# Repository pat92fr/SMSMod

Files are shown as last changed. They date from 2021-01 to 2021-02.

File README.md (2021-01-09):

https://hackaday.io/project/176678-smarter-micro-servo-sms-mod

# SMSMod
 Smarter Micro Servo (SMS) MOD

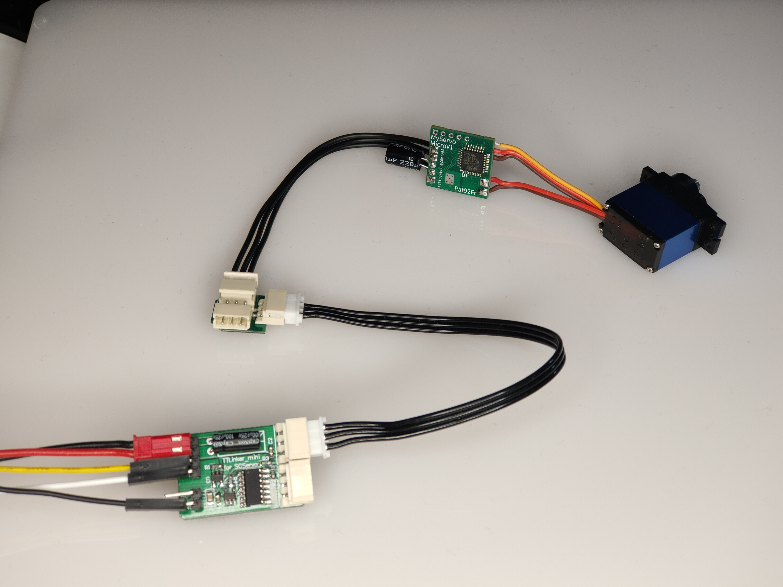
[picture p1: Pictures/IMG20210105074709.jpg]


This projet is a tiny control board for micro servo. It replaces the original servo control board and provides a smart bus interface (TTL level, Up to 1Mbps) and configurable close-loop regulation for robotic applications. Any micro and mini servo may be hacked and driven by this board (5-pin interface : 2 for DC motor, 3 for potentiometer). The control board may be directly powered by a LIPo 2S battery (min 6.5V, max 10V). 

Commercial off-the-shelf smart 3-pin cables, hubs, accessories and physical interface adapter boards (e.g. TTLinker) may be used to connect the hacked servo to the host controller (Arduino board, Arm-based board, RPi, and Jetson). User can drive up to 254 servo, with the same bus.

Position, velocity, and torque of each servo are controlable. Present position, velocity, and torque feedback are avaible. Communication protocol is developed in Python and C/C++ (Arduino). Ping, read, write, sync write, reboot, factory reset commands are supported. One command takes about 1ms to be processed with a return status.

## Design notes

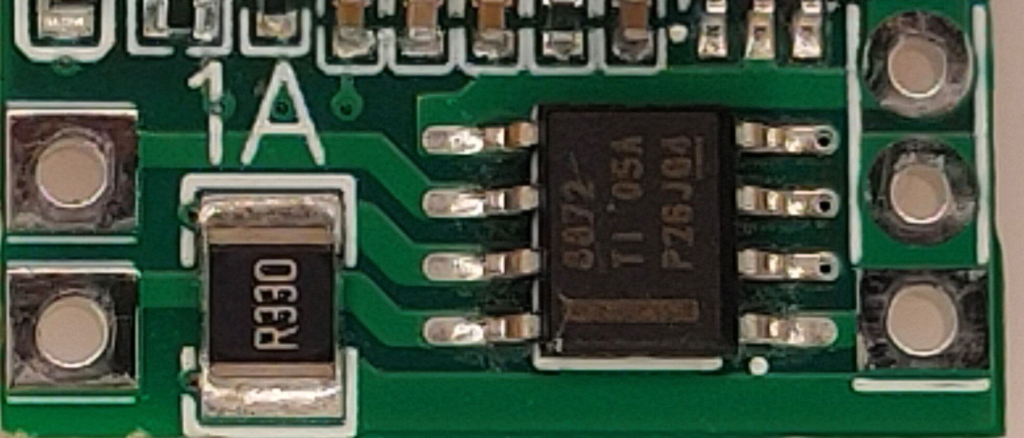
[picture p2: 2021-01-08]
Pictures/IMG20210104151520drv.jpg

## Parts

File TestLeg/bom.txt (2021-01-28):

2x MG92b/MG90s + accessories (screws, arms)
4x printed parts (femur and tibia, supportHipLegx2 one normal, one mirror)
3x screw+bolt M3 x 36mm (for support)
2x rod end bearing M3 x M3 (for linkage knee)
1x rod M3 x 36mm (for linkage knee)
2x 3-part thrust bearing 4x9x4mm (for knee)
1x screw+bolt M3 x 25mm (for knee)
1x M2 x 8 scree (fixing hip servo arm to femur)

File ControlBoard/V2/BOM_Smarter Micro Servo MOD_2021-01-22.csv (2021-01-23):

ID | Name | Designator | Footprint | Quantity | Manufacturer Part | Manufacturer | Supplier | Supplier Part | LCSC Assembly | JLCPCB SMD
1 | 22k | R7,R10 | R0402 | 2 | 0402WGF2202TCE | UniOhm | LCSC | C25768
2 | 2.2k | R3,R11 | R0402 | 2 | 0402WGF2201TCE | UniOhm | LCSC | C25879
3 | 1.5k | R2 | R0402 | 1 | 0402WGF1501TCE | UniOhm | LCSC | C25867
4 | 100k | R6 | R0402 | 1 | 0402WGF1003TCE | UniOhm | LCSC | C25741
5 | 47R | R5 | R0402 | 1 | 0402WGF470JTCE | UniOhm | LCSC | C25118
6 | 200 | R4 | R0402 | 1 | 0402WGF2000TCE | UniOhm | LCSC | C25087
7 | DRV8872DDAR | U3 | HSOP-8_L5.0-W4.0-P1.27-LS6.2-BL-EP | 1 | DRV8872DDAR | TI | LCSC | C114179 | Yes
8 | LED-0603_R | LED2 | LED0603_RED | 1 | 19-213/Y2C-CQ2R2L/3T(CY) | EVERLIGHT | LCSC | C72038
9 | STM32G431K8T6 | U1 | LQFP-32_L7.0-W7.0-P0.80-LS9.0-BL | 1 | STM32G431KBT6 | STMicroelectronics | LCSC | C529357
10 | HDR-M-2.54_1x1 | J4,J3 | HDR-M-2.54_1X1 | 2 |  |  | LCSC | C81276
11 | 0.33R | R1 | R1210 | 1 | 1210W2F330LT5E | Uniroyal Elec | LCSC | C95211 | Yes
12 | TLV70433DBVT | U2 | TSOT-23-5_L2.9-W1.6-P0.95-LS2.8-BR | 1 | TLV70433DBVT | Texas Instruments | LCSC | C94776 |  | Yes
13 | 10uH | L1 | L0603 | 1 | LBMF1608T100K | TAIYO YUDEN | LCSC | C87216
14 | HDR-F-2.54_1x3 | H3 | HDR-F-2.54_1X3 | 1 |  |  | LCSC | C146690
15 | HDR-M-2.54_1x5 | J2,J1 | HDR-M-2.54_1X5 | 2 |  |  | LCSC | C358687
16 | NC7SP125P5X | U6,U5 | SC-70-5_L2.1-W1.3-P0.65-LS2.1-BR | 2 | NC7SP125P5X | ON Semicon | LCSC | C184652 | Yes
17 | 100nF | C5,C4,C10,C9,C7,C3 | C0402 | 6 | CL05B104KO5NNNC | SAMSUNG | LCSC | C1525
18 | 1nF | C13 | C0402 | 1 | 0402B102K500NT | FH | LCSC | C1523
19 | 1uF | C12,C1 | C0402 | 2 | CL05A105KA5NQNC | SAMSUNG | LCSC | C52923
20 | 10nF | C11 | C0402 | 1 | CL05B103KB5NNNC | SAMSUNG | LCSC | C15195
21 | 4.7uF | C8,C2 | C0402 | 2 | CL05A475MP5NRNC | SAMSUNG | LCSC | C23733

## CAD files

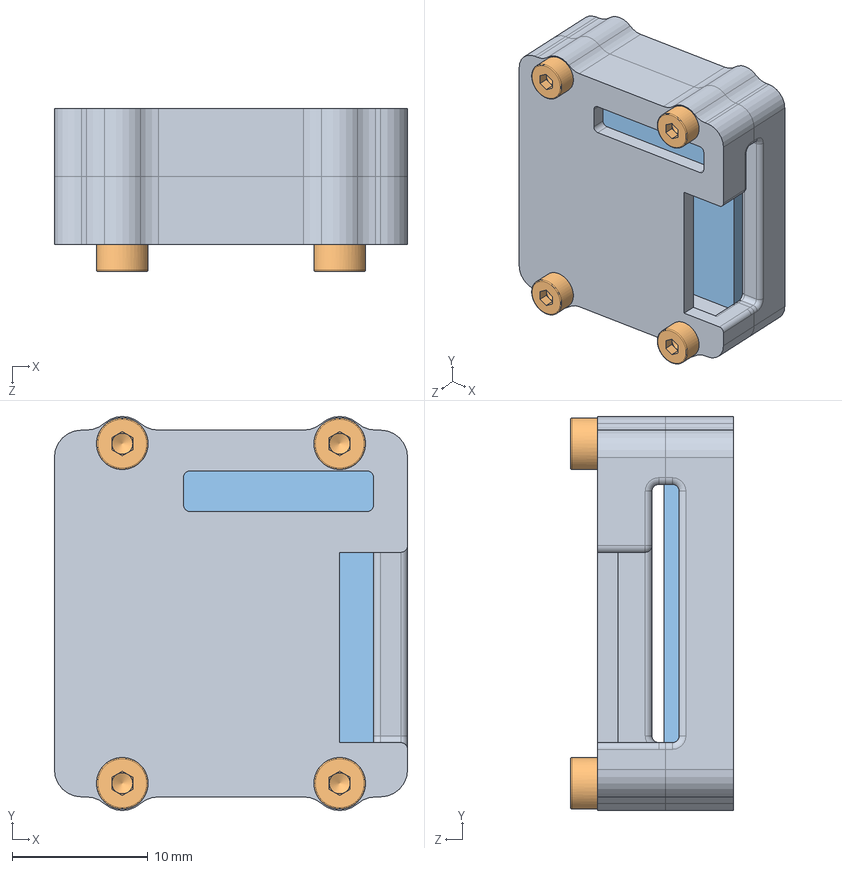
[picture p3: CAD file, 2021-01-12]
ControlBoard/CASE/Assemblage.SLDASM
26.0 x 29.0 x 12.0 mm
case x 2
socket head cap screw_iso x 4
PCB

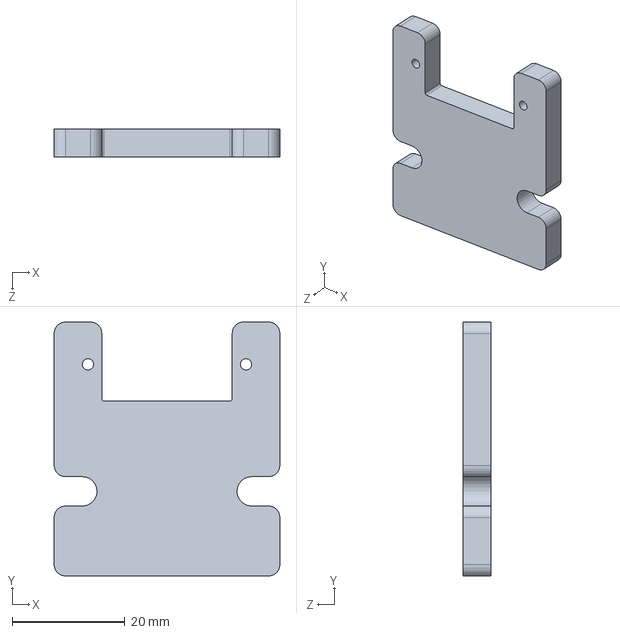
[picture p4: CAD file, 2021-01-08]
ControlBoard/MECA/supportMicro.SLDPRT
40.0 x 45.0 x 5.00 mm

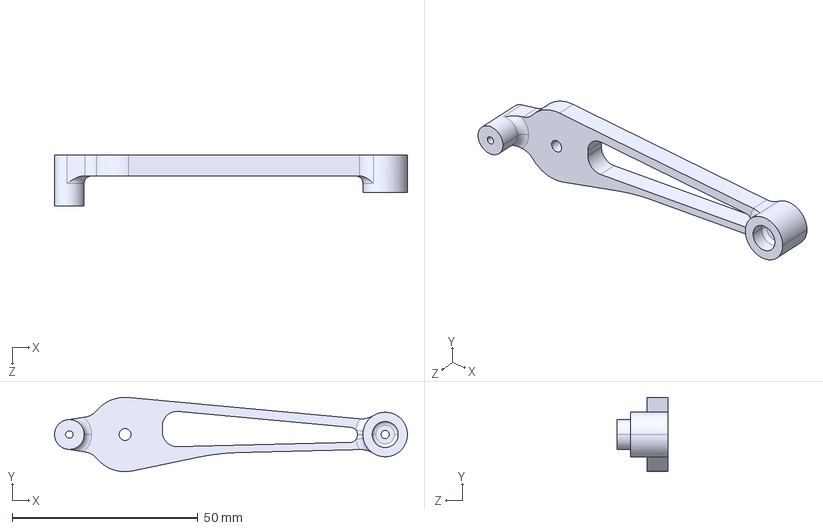
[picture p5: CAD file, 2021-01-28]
TestLeg/Tibia3.STEP
95.0 x 20.0 x 13.6 mm

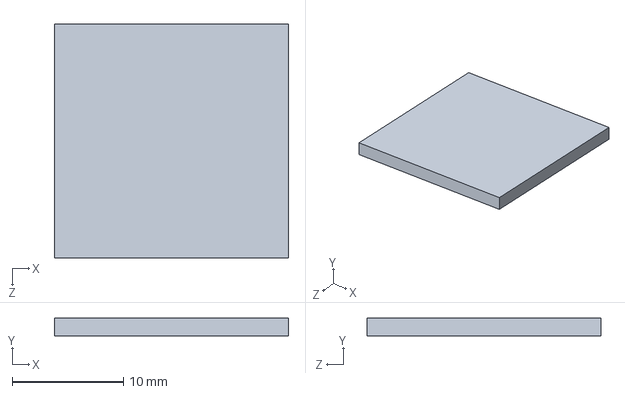
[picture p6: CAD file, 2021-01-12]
ControlBoard/CASE/PCB.SLDPRT
21.0 x 1.60 x 21.0 mm

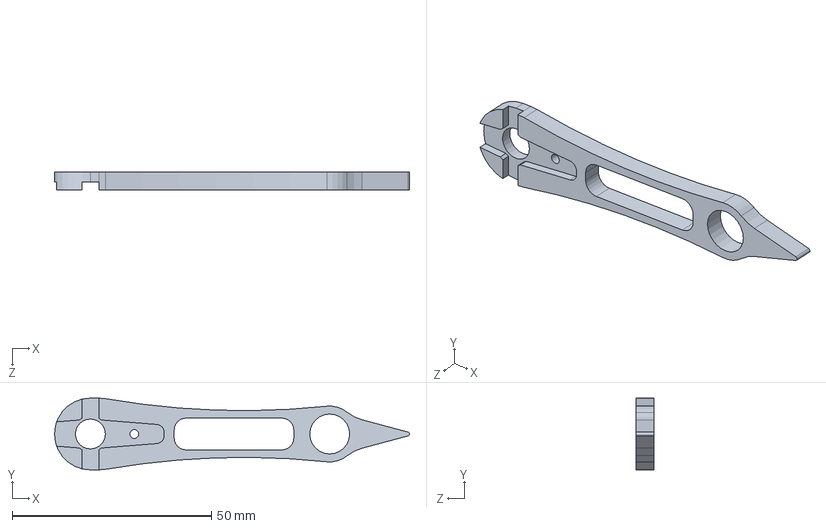
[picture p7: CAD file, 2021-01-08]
ControlBoard/MECA/Arm.SLDPRT
89.0 x 18.0 x 4.60 mm

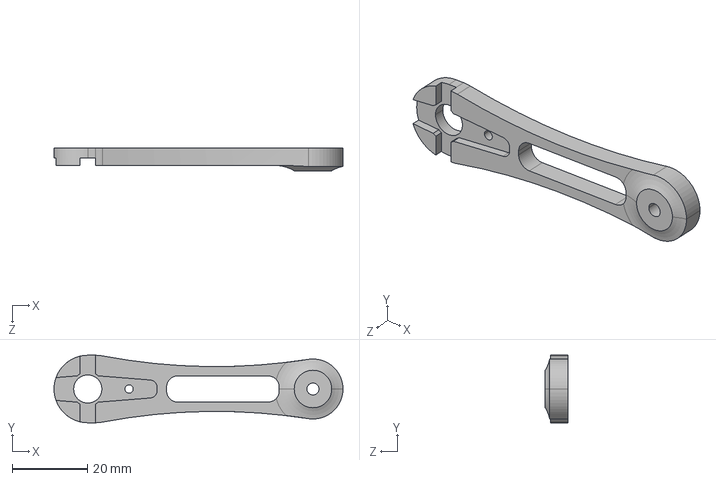
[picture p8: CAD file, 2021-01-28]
TestLeg/Femur4.STEP
77.0 x 18.0 x 6.00 mm

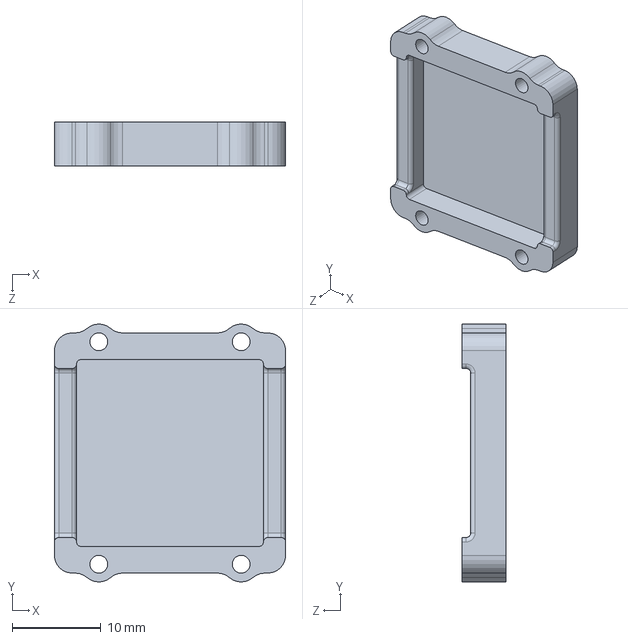
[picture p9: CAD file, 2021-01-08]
ControlBoard/CASE/case.SLDPRT
26.0 x 29.0 x 5.00 mm

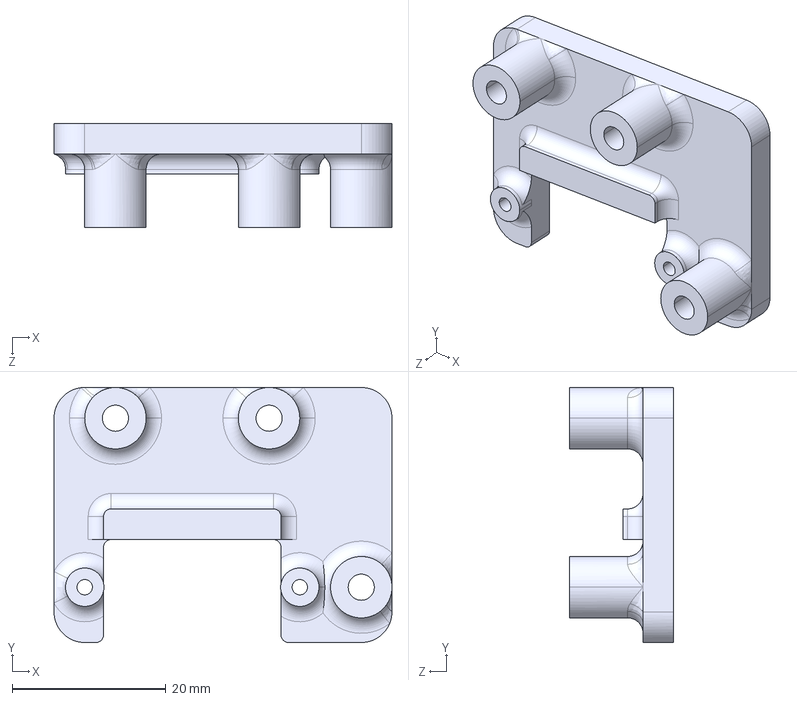
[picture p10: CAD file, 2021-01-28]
TestLeg/supportHipLeg.STEP
44.0 x 33.2 x 13.6 mm

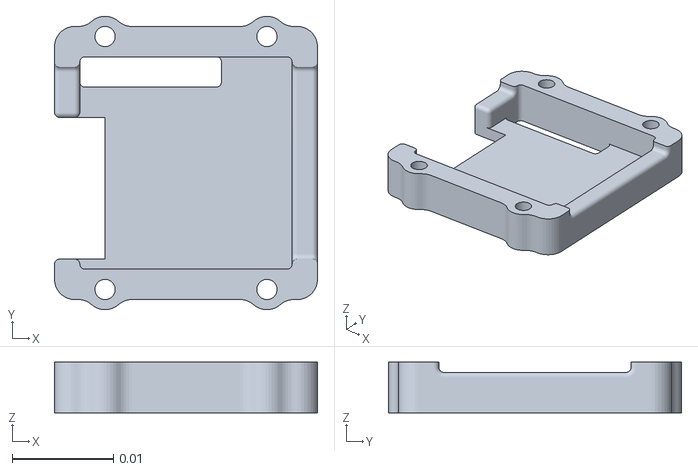
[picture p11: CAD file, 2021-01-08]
ControlBoard/CASE/caseTOP.STL
0.026 x 0.029 x 0.005

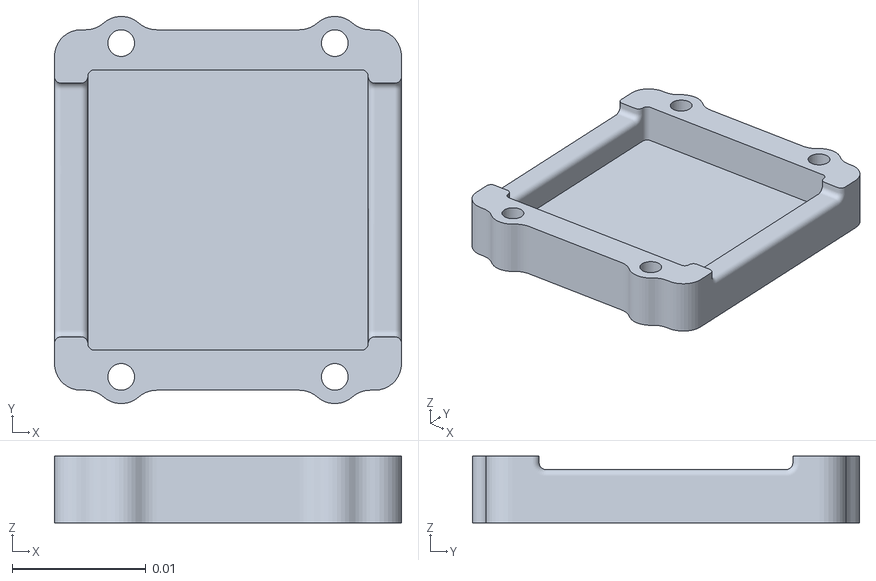
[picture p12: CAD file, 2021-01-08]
ControlBoard/CASE/caseBOTTOM.STL
0.026 x 0.029 x 0.005

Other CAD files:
ControlBoard/MECA/Arm.STL
TestLeg/Femur4.STL
TestLeg/Tibia3.STL
TestLeg/supportHipLeg.STL

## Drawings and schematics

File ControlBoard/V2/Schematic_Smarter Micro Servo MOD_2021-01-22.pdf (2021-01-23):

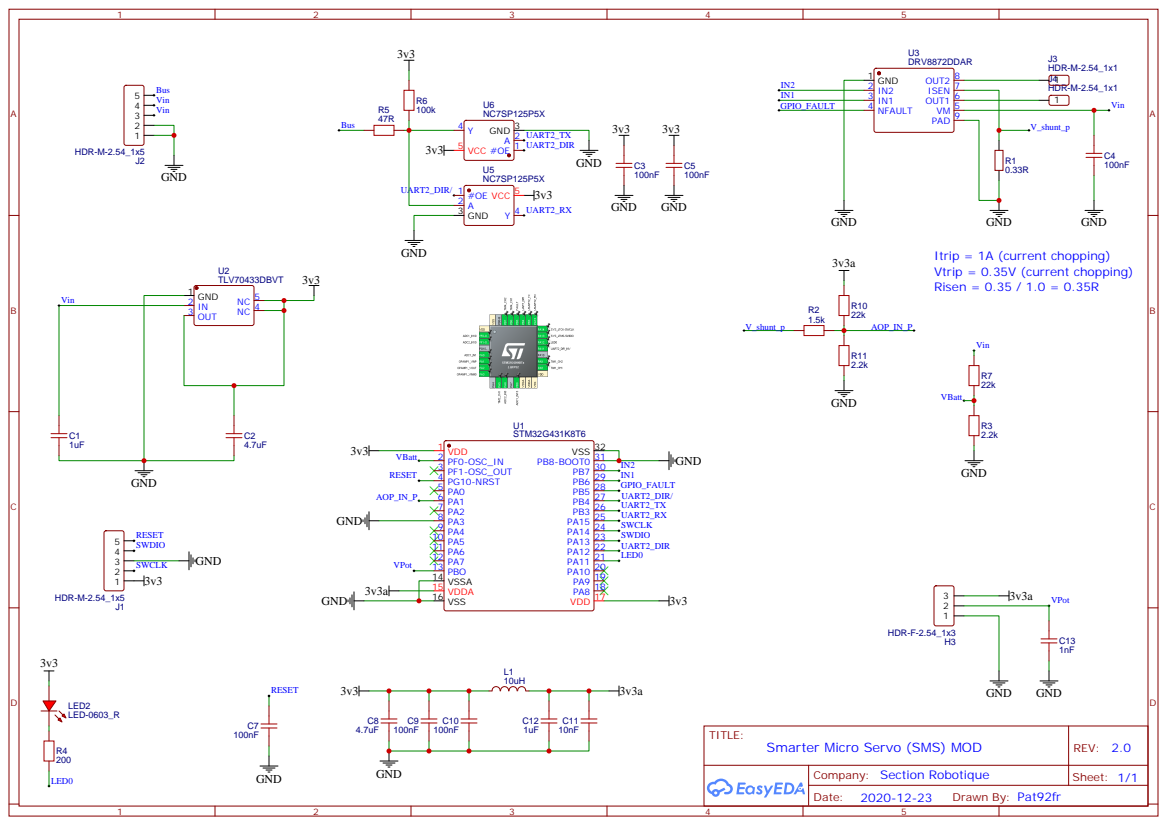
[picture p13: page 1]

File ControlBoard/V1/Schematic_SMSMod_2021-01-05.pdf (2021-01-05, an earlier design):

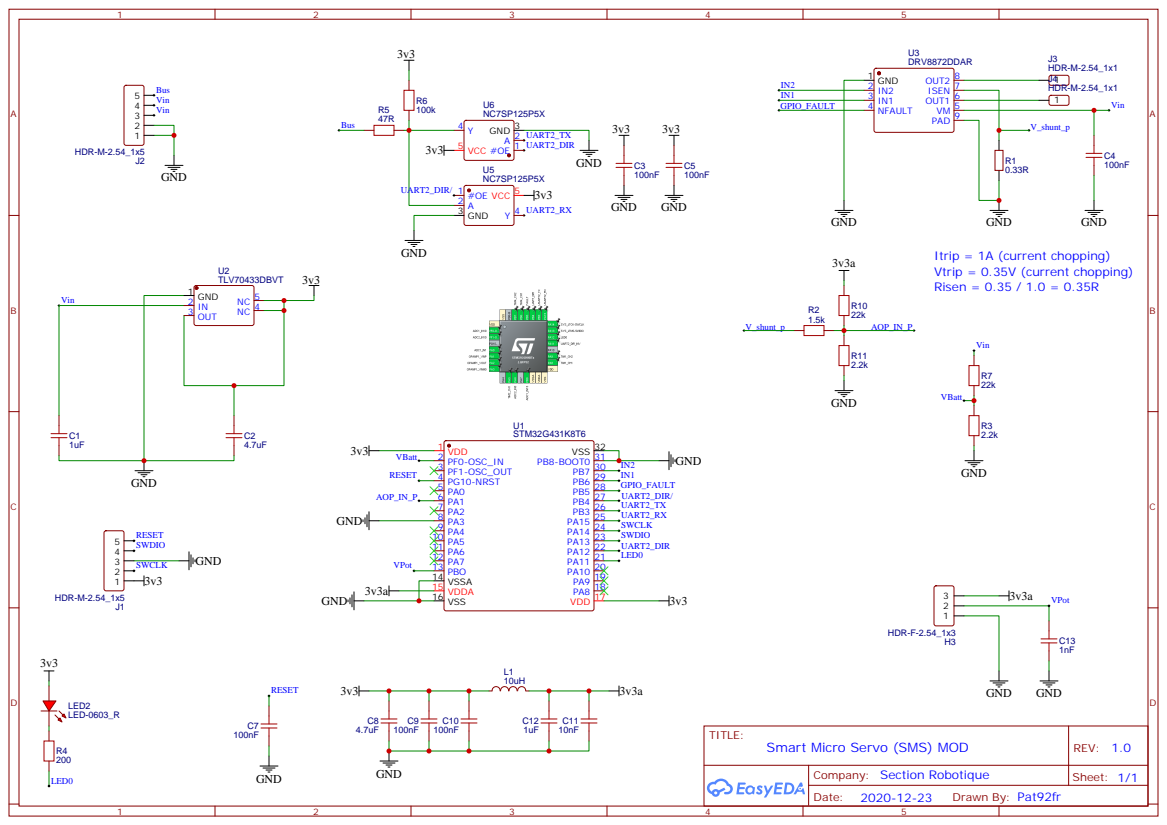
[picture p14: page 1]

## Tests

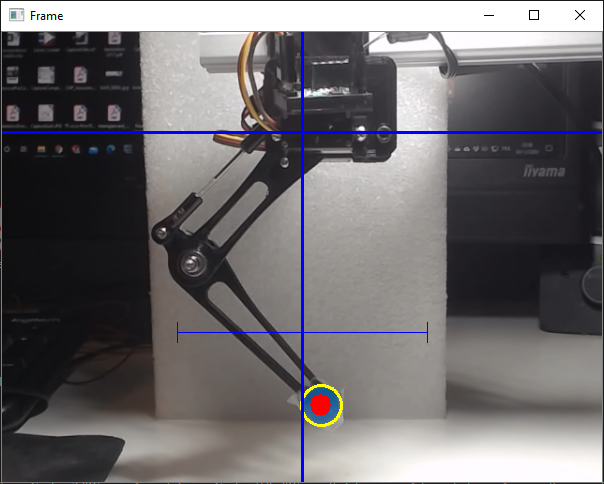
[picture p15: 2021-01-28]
TestLeg/CaptureV1.PNG

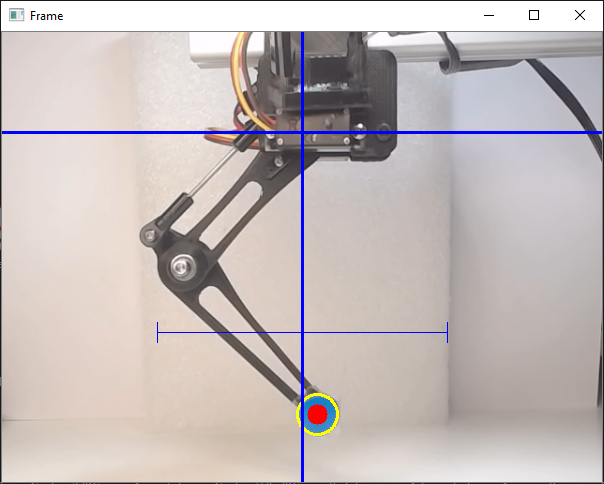
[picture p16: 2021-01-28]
TestLeg/CaptureV1b.PNG

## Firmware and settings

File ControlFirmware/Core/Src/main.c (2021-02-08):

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
/* Includes ------------------------------------------------------------------*/
#include "main.h"

/* USER CODE BEGIN Includes */
#include "led.h"
#include "serial.h"
#include "eeprom.h"
#include "control_table.h"
#include "control_algo.h"
#include "protocol.h"
/* USER CODE END Includes */

ADC_HandleTypeDef hadc1;
DMA_HandleTypeDef hdma_adc1;

OPAMP_HandleTypeDef hopamp1;

TIM_HandleTypeDef htim4;
TIM_HandleTypeDef htim15;

UART_HandleTypeDef huart2;
DMA_HandleTypeDef hdma_usart2_rx;
DMA_HandleTypeDef hdma_usart2_tx;

/* USER CODE BEGIN PV */
HAL_Serial_Handler serial;

/* USER CODE END PV */

void SystemClock_Config(void);
static void MX_GPIO_Init(void);
static void MX_DMA_Init(void);
static void MX_TIM4_Init(void);
static void MX_TIM15_Init(void);
static void MX_USART2_UART_Init(void);
static void MX_ADC1_Init(void);
static void MX_OPAMP1_Init(void);
/**
  * @brief  The application entry point.
  * @retval int
  */
int main(void)
{
  /* MCU Configuration--------------------------------------------------------*/

  /* Reset of all peripherals, Initializes the Flash interface and the Systick. */
  HAL_Init();

  /* Configure the system clock */
  SystemClock_Config();

  /* Initialize all configured peripherals */
  MX_GPIO_Init();
  MX_DMA_Init();
  MX_TIM4_Init();
  MX_TIM15_Init();
  MX_USART2_UART_Init();
  MX_ADC1_Init();
  MX_OPAMP1_Init();
  /* USER CODE BEGIN 2 */
  HAL_Led_Init();
  HAL_Led_Blink(LED0,10,150);
  HAL_Serial_Init_Half_Duplex(
	&huart2,
	&serial,
	UART2_DIR_TX_GPIO_Port,
	UART2_DIR_TX_Pin,
	GPIO_PIN_RESET,
	UART2_DIR_RX_GPIO_Port,
	UART2_DIR_RX_Pin,
	GPIO_PIN_RESET
	);
	if(eeprom_empty())
		factory_reset_eeprom_regs();
	load_eeprom_regs();
	reset_ram_regs();
	APP_Control_Init();
  /* USER CODE END 2 */

  /* Infinite loop */
  /* USER CODE BEGIN WHILE */
  uint32_t start_time = HAL_GetTick();
  while (1)
  {
    /* USER CODE END WHILE */

    /* USER CODE BEGIN 3 */

	  // Handle LED
	if(HAL_GetTick()>start_time+2000) // blink first 2 seconds
	{
		if(regs[REG_LED]==0)
		{
			HAL_Led_Reset(LED0);
		}
		else if(regs[REG_LED]==1)
		{
			HAL_Led_Set(LED0);
		}
	}
	HAL_Led_Process();

	// Handle communication
	while(HAL_Serial_Available(&serial))
	{
	  char c = HAL_Serial_GetChar(&serial);
	  packet_handler(c);
	}

	// regulation
	APP_Control_Process();

  }
  /* USER CODE END 3 */
}

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


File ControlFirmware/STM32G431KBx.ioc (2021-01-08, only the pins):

Mcu.UserName=STM32G431KBTx
PA1.Signal=OPAMP1_VINP
PA11.GPIO_Label=LED0
PA11.Signal=GPIO_Output
PA12.GPIO_Label=UART2_DIR_TX
PA12.Signal=GPIO_Output
PA13.Signal=SYS_JTMS-SWDIO
PA14.Signal=SYS_JTCK-SWCLK
PA15.Signal=USART2_RX
PA3.Signal=OPAMP1_VINM0
PB0.Signal=ADC1_IN15
PB3.Signal=USART2_TX
PB4.GPIO_Label=UART2_DIR_RX
PB4.Signal=GPIO_Output
PB5.GPIO_Label=FAULT
PB5.Signal=GPIO_Input
PB6.Signal=S_TIM4_CH1
PB7.Signal=S_TIM4_CH2
PF0-OSC_IN.Signal=ADC1_IN10

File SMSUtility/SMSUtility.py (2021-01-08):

import time

import serial
# help : https://pythonhosted.org/pyserial/pyserial_api.html

from tkinter import *
#from tkinter.ttk import *

from id_frame import *
from eeprom_frame import *
from ram_frame import *
from trace_frame import *
from protocol2 import *

import cProfile


def main():

	servo = servo_protocol2('COM3',500000) ##eeprom baud = 3

	window = Tk()
	window.title(" MyServoGUI")
	window.geometry("1600x1020")
	window.minsize(1600,1020)

	fi = id_frame(window,servo)
	fe = eeprom_frame(window,servo,fi)
	ft =trace_frame(window,servo,fi)
	fr = ram_frame(window,servo,ft,fi)

	fi.grid(column = 0, row = 0, sticky='nsew')		
	fe.grid(column = 1, row = 0, sticky='nsew')		
	ft.grid(column = 2, row = 0, sticky='nsew')		
	fr.grid(column = 3, row = 0, sticky='nsew')		
		
	window.columnconfigure(2, weight=1)
	window.rowconfigure(0, weight=1)

	mainloop()


if __name__ == "__main__":

	##cProfile.run("main()")
	main()

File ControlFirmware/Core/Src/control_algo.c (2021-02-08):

/*
 * control_algo.c
 *
 *  Created on: 6 nov. 2020
 *      Author: Patrick
 */

#include "control_algo.h"
#include "control_table.h"
#include "math_tool.h"
#include "binary_tool.h"
#include "pid.h"

#include <stdbool.h>
#include <math.h>

// Public variables
extern TIM_HandleTypeDef htim4;
extern TIM_HandleTypeDef htim15;
extern ADC_HandleTypeDef hadc1;
extern OPAMP_HandleTypeDef hopamp1;

// CONTROL LOOP
#define LOOP_FREQUENCY_HZ 1000.0f //Hz

// MOTOR
#define MOTOR_PWM_BRAKE 99
#define MOTOR_PWM_COAST 0

// POSITION FILTER
#define ALPHA_POSITION				0.05f // (default:0.05) F = 20kHz ==> Fc (-3dB) = 170.0Hz
#define ALPHA_VOLTAGE				0.05f // (default:0.05) F = 20kHz ==> Fc (-3dB) = 170.0Hz
#define ALPHA_CURRENT_SENSE			0.05f // (default:0.05) F = 20kHz ==> Fc (-3dB) = 170.0Hz
#define ALPHA_CURRENT_SENSE_OFFSET 	0.001f


#define ALPHA_VELOCITY			0.12f // (default:0.12) F = 1000Hz ==> Fc (-3dB) = 20Hz
#define ALPHA_CURRENT_SETPOINT 	0.96f // (default:0.12) F = 1000Hz ==> Fc (-3dB) = 20Hz
#define ALPHA_PWM_SETPOINT		0.12f // (default:0.12) F = 1000Hz ==> Fc (-3dB) = 20.0Hz
#define VOLTAGE_CALIBRATION 	1.08f

// Private Variables

// raw sensor inputs
volatile uint16_t ADC_DMA[3] = { 0,0,0 };
// filtered sensor inputs
static float motor_current_input_adc = 0.0f;
static float position_input_adc = 0.0f;
static float voltage_input_adc = 0.0f;
static float motor_current_input_adc_offset = 0.0f;
static float pwm_sign = 0.0f;
static float pwm_ratio = 0.0f;
// scaled sensor inputs
static float present_motor_current_ma = 0.0f;
static float present_position_deg = 0.0f;
static float present_voltage_0v1 = 0.0f;
// setpoints
static float setpoint_pwm = 0.0f;
static float setpoint_current_ma = 0.0f;
static float setpoint_acceleration_dpss = 0.0f;
static float setpoint_velocity_dps = 0.0f;
static float setpoint_position_deg = 0.0f;
// control loop state
static bool entering_state = true;
static uint32_t current_control_mode = REG_CONTROL_MODE_POSITION_TORQUE;
static uint16_t const period_us = (uint16_t)(1000000.0f/LOOP_FREQUENCY_HZ);
static uint32_t counter = 0;
// PIDs
static pid_context_t pid_position;
static pid_context_t pid_current;
// variables
static float present_velocity_dps = 0.0f;
static float last_present_position_deg = 0.0f;
static float last_setpoint_velocity_dps = 0.0f;

void scale_all_sensors()
{
	// scale motor current sense (unit:mA) and estimated average motor current with sign (using PWM ratio and setpoint PWM sign)
	float const a = (float)(MAKE_SHORT(regs[REG_CAL_CURRENT_SENSE_A_L],regs[REG_CAL_CURRENT_SENSE_A_H]));
	present_motor_current_ma = (motor_current_input_adc-motor_current_input_adc_offset)/a*1000.0f*pwm_sign*pwm_ratio;

	// scale position (unit:degrees)
	float const min_position_adc = (float)(MAKE_SHORT(regs[REG_MIN_POSITION_ADC_L],regs[REG_MIN_POSITION_ADC_H]));
	float const max_position_adc = (float)(MAKE_SHORT(regs[REG_MAX_POSITION_ADC_L],regs[REG_MAX_POSITION_ADC_H]));
	float const max_rotation_deg = (float)(regs[REG_MAX_ROTATION_DEG]);
	present_position_deg = fmap(position_input_adc,min_position_adc,max_position_adc,0.0f,max_rotation_deg);
	// potentiometer leads maybe inverted, user can reverse polarity of potentiometer (EEPROM parameter)
	if(regs[REG_INV_ROTATION_SENSOR] > 0)
		present_position_deg =  max_rotation_deg-present_position_deg;

	// scale voltage (unit:0.1V)
	present_voltage_0v1 = voltage_input_adc/4096.0f*3.3f*24.2f/2.2f*10.0f*VOLTAGE_CALIBRATION;
}

// called once after SW REBBOT or HW RESET, and every time entering a new control loop mode
void APP_Control_Reset()
{
	// reset
	entering_state = true;
	counter = 0;
	pid_reset(&pid_position);
	pid_reset(&pid_current);
	setpoint_pwm = 0.0f;
	setpoint_current_ma = 0.0f;
	setpoint_acceleration_dpss = 0.0f;
	setpoint_velocity_dps = 0.0f;
	last_setpoint_velocity_dps = 0.0f;
	setpoint_position_deg = present_position_deg;
	last_present_position_deg = present_position_deg;
	// when re-entering in the control mode 'position', avoid glitch from past goal position
	regs[REG_GOAL_POSITION_DEG_L] = LOW_BYTE((int16_t)(present_position_deg*10.0f));
	regs[REG_GOAL_POSITION_DEG_H] = HIGH_BYTE((int16_t)(present_position_deg*10.0f));
}

// called once after SW REBOOT or HW RESET
void APP_Control_Init()
{
	// reset (EWMA) filtered sensor inputs
	motor_current_input_adc = 0.0f;
	position_input_adc = 0.0f; // NOTE : init by zero will delay the present position estimation by 1 ms at least
	voltage_input_adc = 0.0f; // NOTE : init by zero will delay the present voltage estimation by 1 ms at least
	motor_current_input_adc_offset = (float)(MAKE_SHORT(regs[REG_CAL_CURRENT_SENSE_B_L],regs[REG_CAL_CURRENT_SENSE_B_H]));

	// force motor in coast
	__HAL_TIM_SET_COMPARE(&htim4,TIM_CHANNEL_1,MOTOR_PWM_COAST);
	__HAL_TIM_SET_COMPARE(&htim4,TIM_CHANNEL_2,MOTOR_PWM_COAST);
	// start motor PWM generation
	HAL_TIM_PWM_Start_IT(&htim4,TIM_CHANNEL_1);
	HAL_TIM_PWM_Start_IT(&htim4,TIM_CHANNEL_2);
	HAL_TIM_Base_Start(&htim15);
	// start OP AMP
	HAL_OPAMP_Start(&hopamp1);
	// start ADC
	HAL_ADC_Start_DMA(&hadc1,(uint32_t*)ADC_DMA,3);

	// 2ms delay for filtered sensor inputs to stabilize
	HAL_Delay(1);
	scale_all_sensors();
	HAL_Delay(1);
	scale_all_sensors();

	// reset all state control loop variables
	APP_Control_Reset();
}
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

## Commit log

2021-01-09 EX3 StallGuard example
2021-01-10 gripper demo
2021-01-28 leg mechanics
    [Femur4.STEP, Femur4.STL, Tibia3.STEP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]

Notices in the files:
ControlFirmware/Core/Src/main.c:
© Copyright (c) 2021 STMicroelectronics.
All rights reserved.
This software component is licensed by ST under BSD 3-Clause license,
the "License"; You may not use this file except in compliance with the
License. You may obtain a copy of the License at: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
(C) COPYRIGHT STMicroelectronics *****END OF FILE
